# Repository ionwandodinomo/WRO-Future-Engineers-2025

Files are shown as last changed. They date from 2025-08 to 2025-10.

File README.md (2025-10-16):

<br>

Engineering Documentation 🛠️
======

<br>

> This repository details Team Tralalerotralala's building and programming process in the 2025 WRO Future Engineers Competition.

---

<br>

## Content of Repository 📘
* `models` - 3D CAD files
* `others` - Other essential files
* `schemes` - Electrical schematics
* `src` - Main and other programs to run/control software
* `t-photos` - Team photos
* `v-photos` - Robot photos
* `video` - Video demonstration

<br>

## Content of Documentation 📖
* **[The Team](#the-team-boygirlboy)**
* **[Mechanical Breakdown :wrench:](#mechanical-breakdown-wrench)**
  	* [Materials List](#materials-list)
  	* [Printed Parts](#3D-printed-parts)
  	* [Assembly Views](#full-assembly-views)
* **[Mobility Management :car:](#mobility-management-car)**
	* [The Chassis](#the-chassis)
	* [Drive System](#drive-system)
	* [Steer System](#steer-system)
* **[Power and Sense Management :zap:](#power-and-sense-management-zap)**
	* [The Battery](#the-battery)
	* [Electrical Wiring](#electrical-wiring)
	* [The Sensors](#the-sensors)
* **[Software :computer:](#software-computer)**
    * [Sensing](#sensing)
	* [Open Challenge](#open-challenge)
	* [Obstacle Challenge](#obstacle-challenge)
* **[Assembly Instructions](#assembly-instructions)**
* **[Youtube Videos](#youtube-videos)**
<br>

## The Team :boy::girl::boy:
<p align="center">
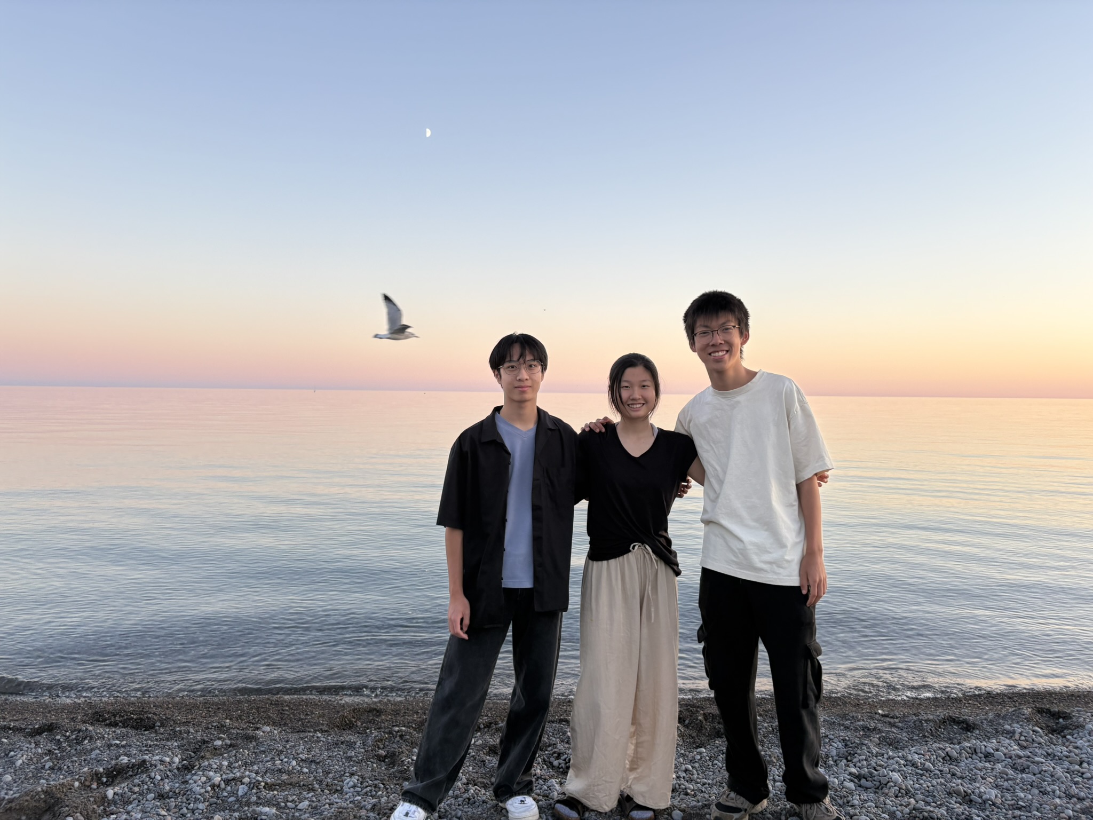
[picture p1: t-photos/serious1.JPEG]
	 
  <br>
  <em>Serious Photo</em>
</p>

### Team Members
 - John Weng (left)
 - Sunni Xue (middle)
 - Eric Rao (right)

|  | Funny Photos |  |
|:---:|:---:|:---:|
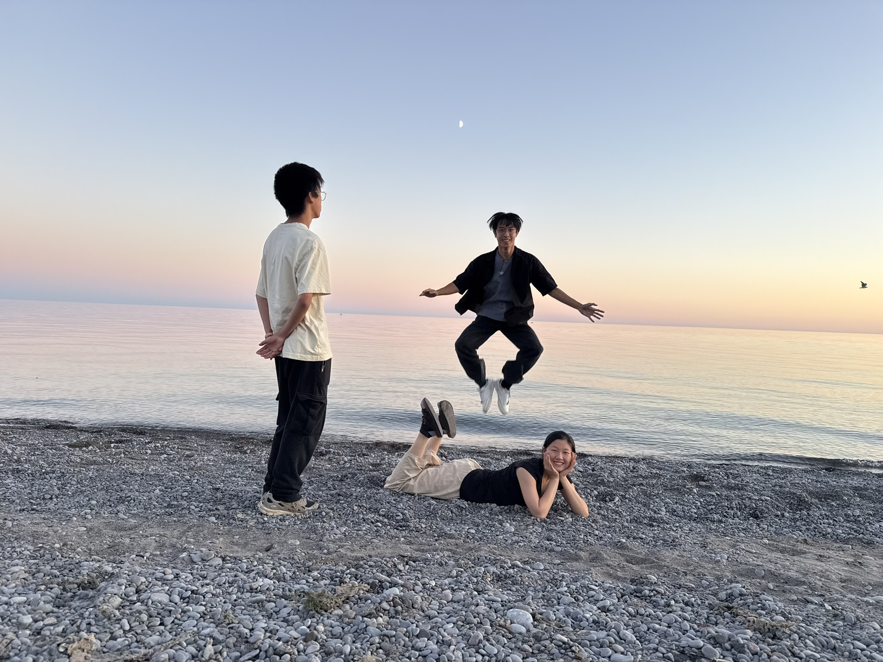
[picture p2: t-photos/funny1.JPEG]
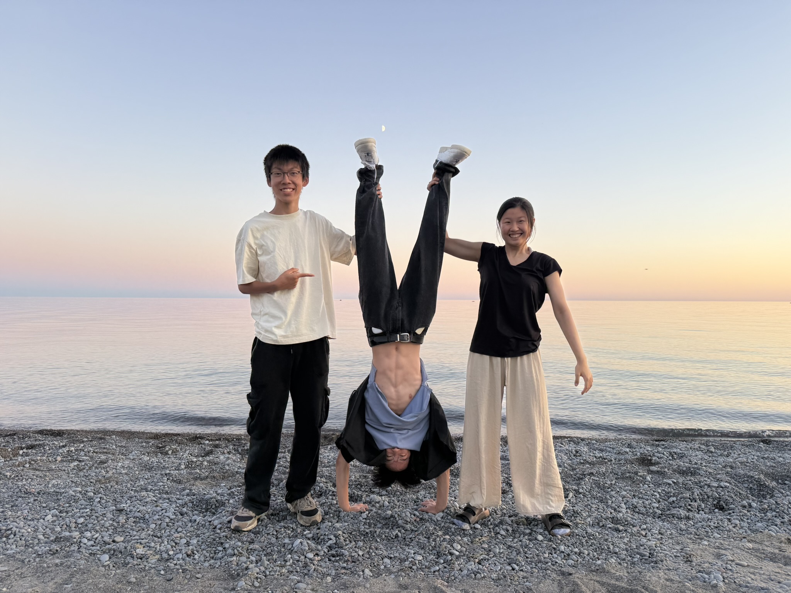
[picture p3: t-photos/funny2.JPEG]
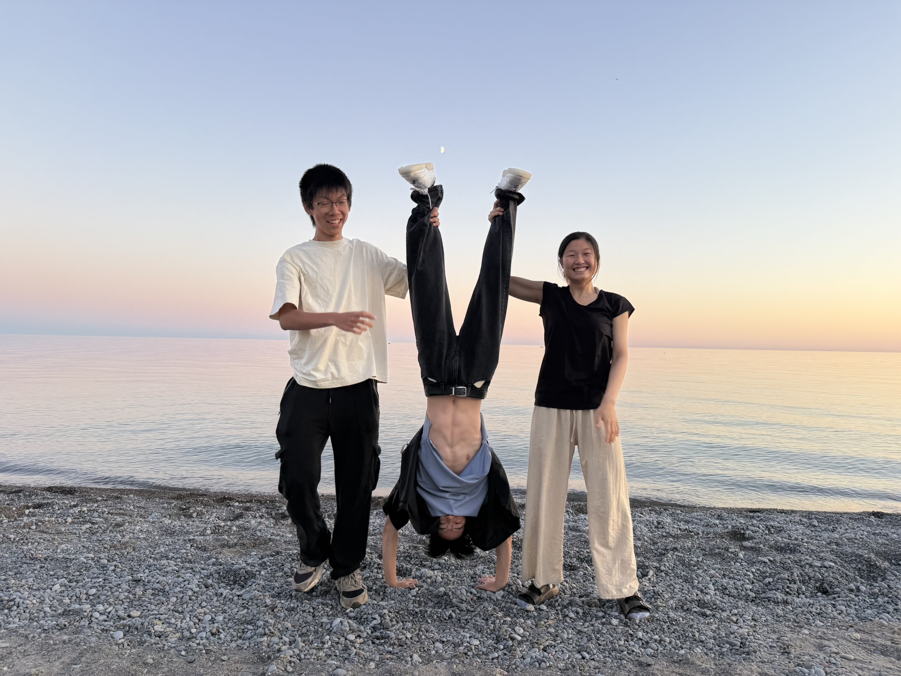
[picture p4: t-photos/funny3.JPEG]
|  |  |  |

<br>

### About us

| Name | About us |
| --- | --- |
| John Weng | Hey! I'm a grade 12 student from Maple High School in Ontario, Canada, and this is my second year doing the Future Engineers Category for WRO. I love messing with mechanics and designing solutions to problems. I love playing sports, especially badminton and volleyball. |
| Sunni Xue | Hi, I'm a grade 11 from the GTA! I've been coding since 6th grade, where I learned Python to build my first project. In my free time, I love playing sports and reading :) |
| Eric Rao | Hello, I am a 12th grade student at Anderson CVI! This is my third year back, and I'm super excited about designing, modelling, and building things. In the future, I hope to pursue mechatronics at the University of Waterloo. |

## Mechanical Breakdown :wrench:

<br>

### Materials List

| Component | Type/Category | Link / Notes |
|:---:|:---:|:---|
| Raspberry Pi 5 (8 GB) | SBC / Processor | — |
| RRC Lite Controller | Controller | [Link](https://www.hiwonder.com/products/rrc-lite?srsltid=AfmBOorP3iSszjlniFgA0gsbfA9aUH3UK0MWuyPeuTUcW6RMQjcizhmE) |
| GT24 B Differential Gear Set | Mechanical / Drive | [Link](https://carisma-shop.com/collections/gt24-spares/products/gt24-b-differential-gear-set) |
| GT24 B Spur Gear 58t | Mechanical / Drive | [Link](https://carisma-shop.com/collections/gt24-spares/products/gt24-b-spur-gear-58t) |
| GT24 SUBARU WRC WHEELS & TIRES SET | Drive | [Link](https://carisma-shop.com/collections/gt24-spares/products/gt24-subaru-wrc-wheels-tires-set-mounted) |
| GT24 WHEEL Outdrive Set | Drive| [Link](https://carisma-shop.com/collections/gt24-spares/products/gt24-b-axle-outdrive-set) |
| GT24 B Plastic Wheel lock nut set | Drive | [Link](https://carisma-shop.com/collections/gt24-spares/products/gt24-b-plastic-screw-on-wheel-nuts-x4) |
| Furitek Micro Komodo 1212 3450KV Brushless Motor | Motor | [Link](https://furitek.com/products/furitek-micro-komodo-1212-3456kv-brushless-motor-with-15t-steel-pinion-for-fury-wagon-fx118) |
| Furiteck Lizard Pro 30A/50A Brushless ESC | ESC | [Link](https://furitek.com/products/combo-of-furitek-lizard-pro-30a-50a-brushed-brushless-esc-for-axial-scx24-with-bluetooth) |
| Gens Ace 2S1P 1300mAh 7.4V battery | Battery | [Link](https://www.adrenalinehobby.com/products/gens-ace-g-tech-1300mah-2s-7-4v-25c-lipo-deans-plug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) |
| Sun Founder SG90 Micro Digital 9G Servo Motor | Servo | [Link](https://www.sunfounder.com/products/sg90-micro-digital-servo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) |
| Mini Rocker Switch | Switch | (Any switch will work) |
| Raspberry Pi Camera Module 8 MP | Sensor / Camera | [Link](https://www.amazon.ca/TUOPUONE-Compatible-Raspberry-MIPI-CSI-Interface/dp/B0CPTPJLXL?th=1) |
| Micro SD card | Storage | — |
| LDRobot LD19 lidar kit | Sensor / Lidar | [Link](https://www.aliexpress.com/item/1005003012681021.html?spm=a2g0o.order_list.order_list_main.11.7a3b18028WK12R) |

<br>

---

<br>

Our car uses primarily **3D printed PLA filament** as the structural material. We used the **[Prusa MK4S](https://www.prusa3d.com/product/original-prusa-mk4s-3d-printer-5/)** from Prusa Research, as well as the ENDER 3 S1. 3D printing allows precise designing of parts, and PLA is readily available and easily accessible for commercial 3D printing. After assessment, it was chosen over other materials such as ABS or PETG. These filaments are also all generally lighter and much more customizable than other common materials, such as LEGO.

<br>

| Material | Pros | Cons |
|---|---|---|
| **PLA** | - Easy to print<br>- Accurate <br>- Available<br>- Good surface finish | - Brittle<br>- Low heat resistance|
| **ABS** | - Strong<br>- Heat resistant<br>- Slightly flexible | - Warps easily<br>- Emits fumes<br>- Harder to print |
| **PETG** | - Strong<br>- Decent heat resistance<br>| - Stringing issues<br>- Slower prints<br>- Less precise |
| **Nylon** | - Very durable| - Hard to print<br>- Hygroscopic (*retains moisture*) <br>- High temp needed |
| **Carbon Fiber Filaments** | - Rigid<br>- Lightweight<br>- Strong | - Expensive<br>- Requires special setup<br>- Brittle |

<br>

In this particular environment, the cons of PLA aren't drastically impactful. The robot will not have to endure high temperatures, and load-bearing/flexibility is not a priority.

<br>

--- 

<br>

Our CAD softwares of choice were **[Onshape](https://www.onshape.com/en/)**, as well as **[TinkerCAD](https://www.tinkercad.com/)** for simpler geometry. We strongly recommend these two softwares programs for basic component design, as they are generally easy to learn, and provide convenient online cloud storage.

Provided below are models of the 3D printed parts, individually, as well as on the final car. Note the .stl files can all be found in the `models` folder of this repository.

<br>


### 3D Printed Parts  

<table>
  <tr>
    <td align="center" width="25%">
      <b>Axel Servo Holder</b><br>
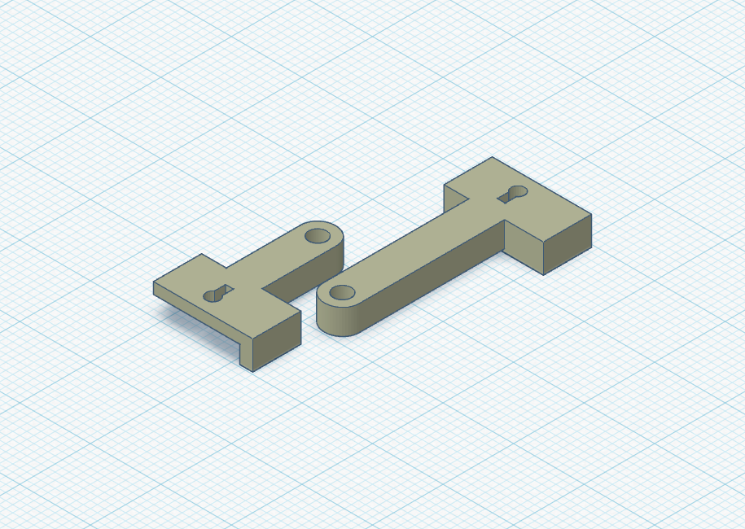
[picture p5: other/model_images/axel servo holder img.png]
      
    </td>
    <td align="center" width="25%">
      <b>Base Plate</b><br>
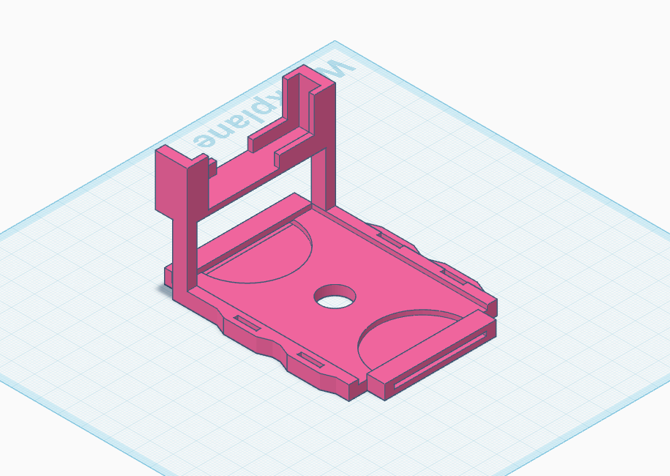
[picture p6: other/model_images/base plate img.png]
      
    </td>
    <td align="center" width="25%">
      <b>Battery Bracket</b><br>
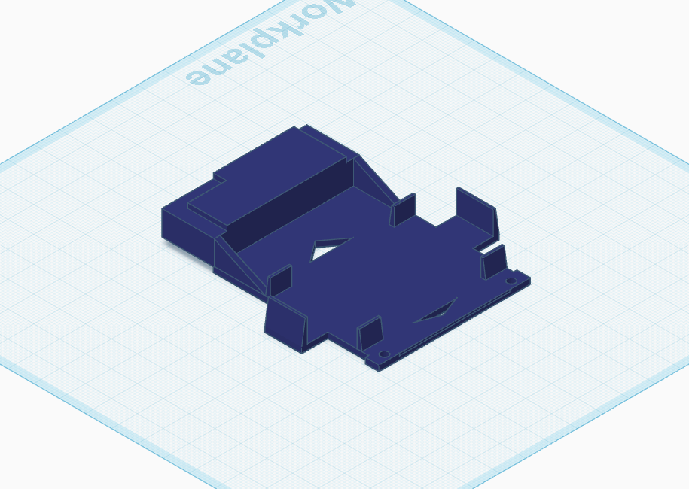
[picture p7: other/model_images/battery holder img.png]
      
    </td>
    <td align="center" width="25%">
      <b>Camera Bracket</b><br>
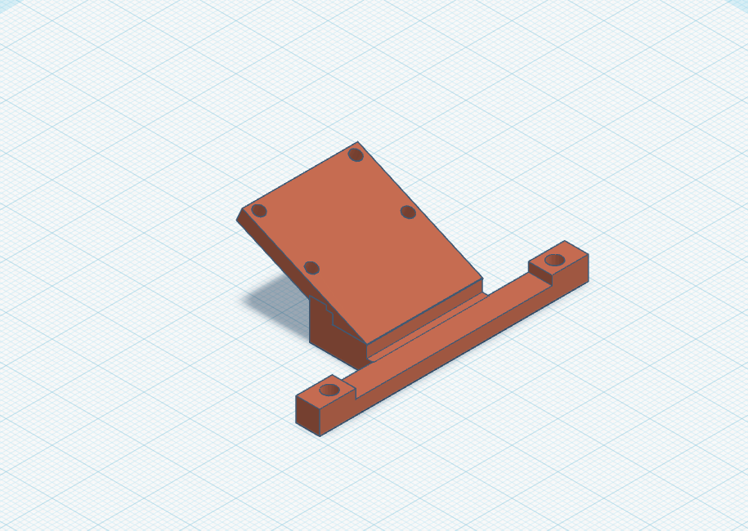
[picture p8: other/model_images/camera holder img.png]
      
    </td>
  </tr>
  <tr>
    <td align="center" width="25%">
      <b>Chassis Pin</b><br>
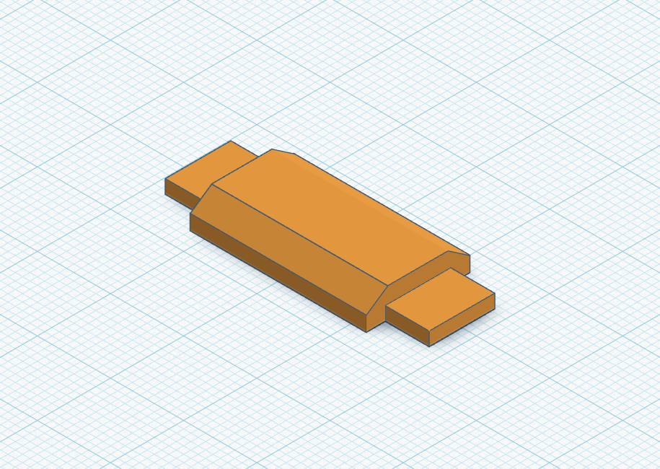
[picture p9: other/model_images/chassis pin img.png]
      
    </td>
    <td align="center" width="25%">
      <b>Differential Cover</b><br>
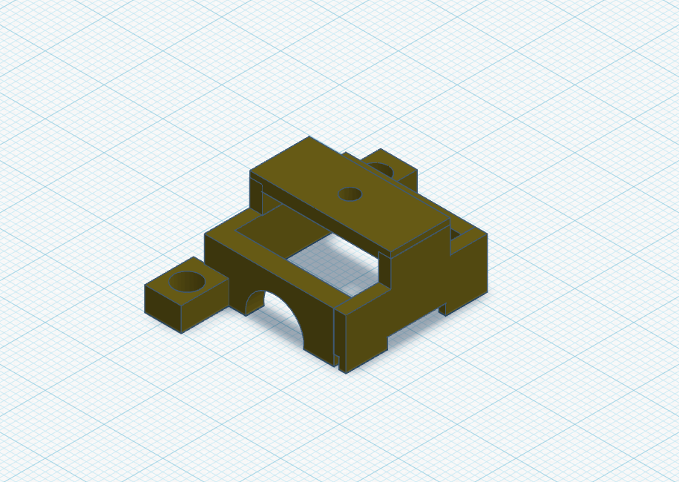
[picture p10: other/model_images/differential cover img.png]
      
    </td>
    <td align="center" width="25%">
      <b>Front Axel</b><br>
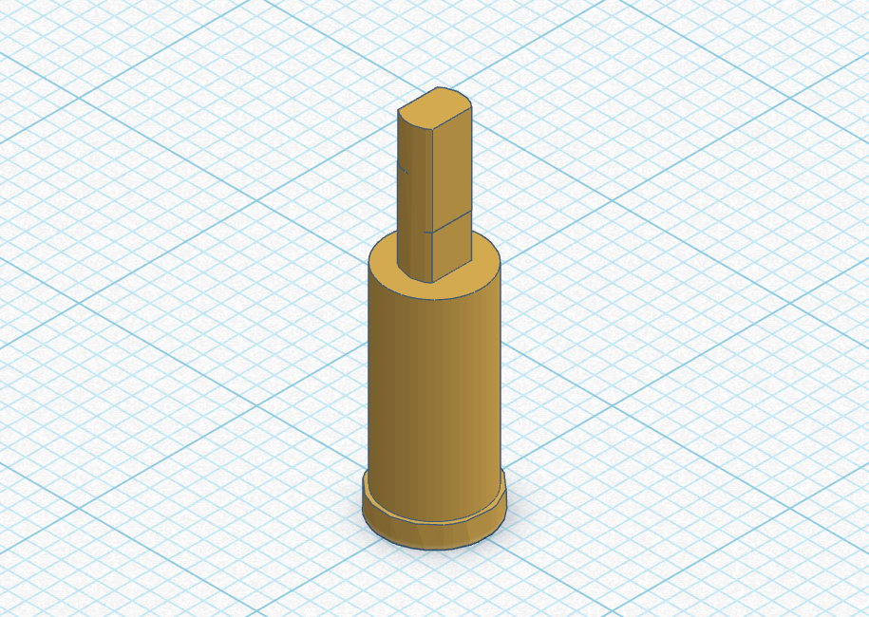
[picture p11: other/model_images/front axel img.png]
      
    </td>
    <td align="center" width="25%">
      <b>Motor Gear Bracket</b><br>
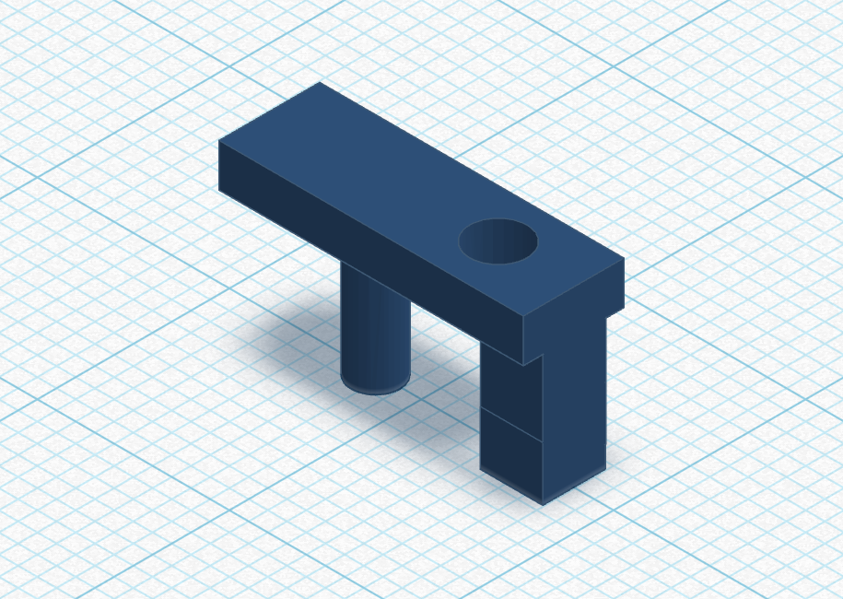
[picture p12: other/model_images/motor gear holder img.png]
      
    </td>
  </tr>
  <tr>
    <td align="center" width="25%">
      <b>Rear Motor Stand</b><br>
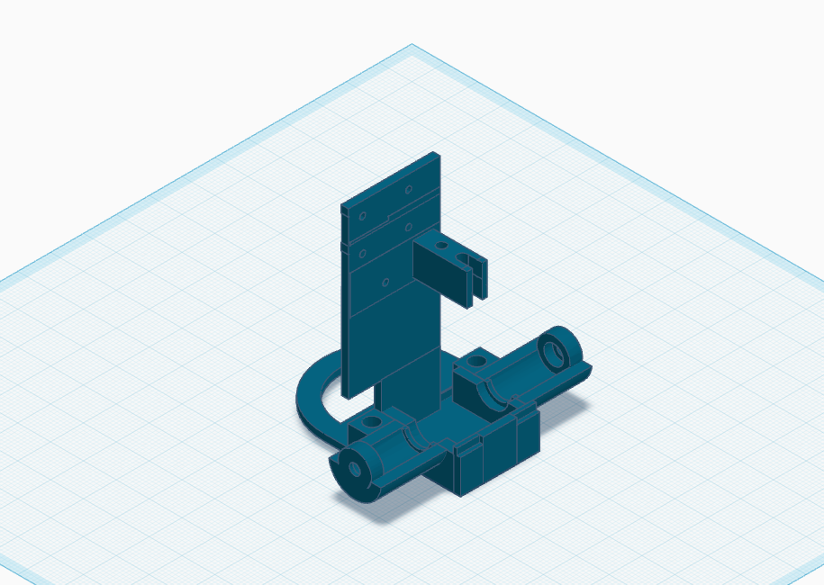
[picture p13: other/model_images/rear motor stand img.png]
      
    </td>
    <td align="center" width="25%">
      <b>RPI Base</b><br>
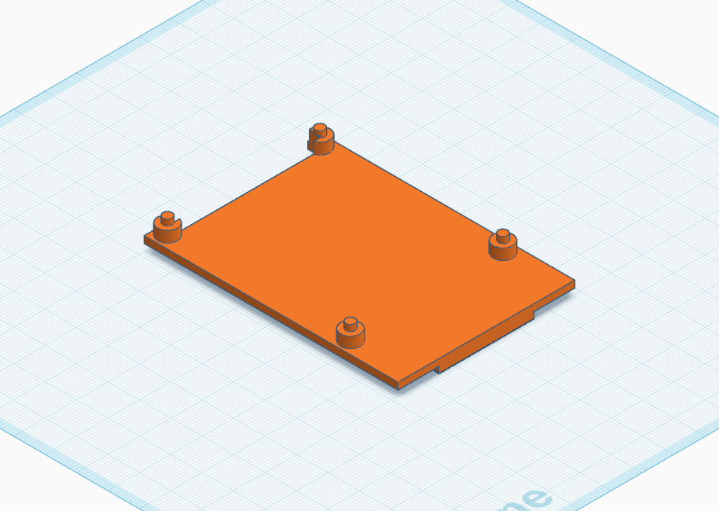
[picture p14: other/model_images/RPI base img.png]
      
    </td>
    <td align="center" width="25%">
      <b>RPI HAT Bracket</b><br>
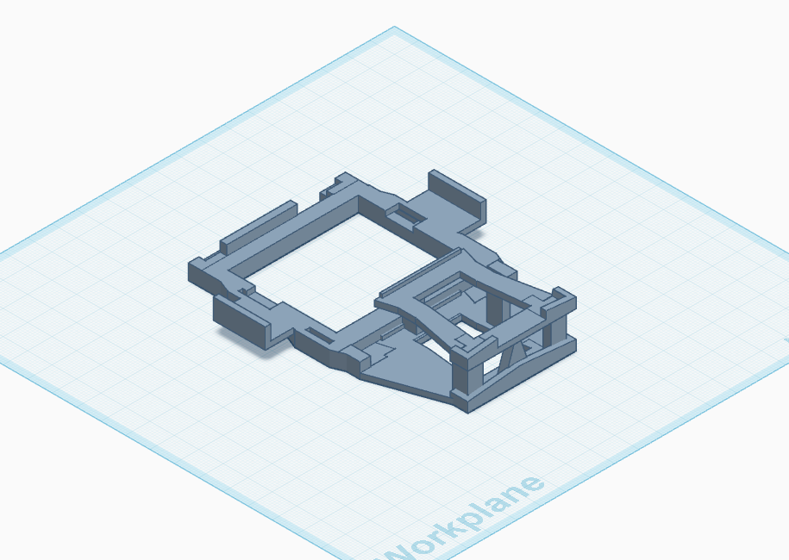
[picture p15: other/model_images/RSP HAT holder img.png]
      
    </td>
    <td align="center" width="25%">
      <b>Servo Stand<b><br>
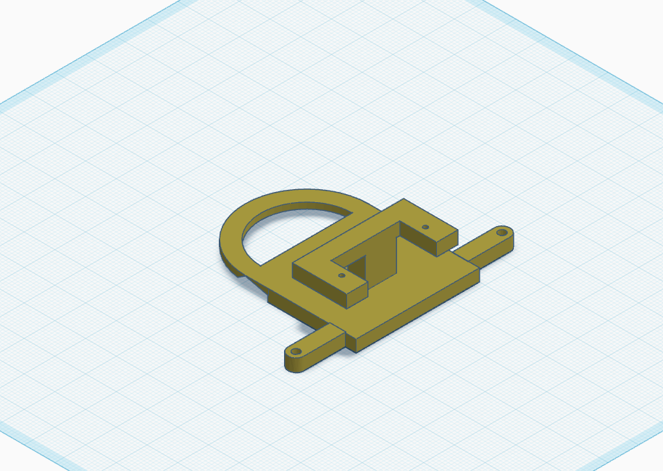
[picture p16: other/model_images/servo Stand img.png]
      
    </td>
  </tr>
  <tr>
    <td align="center" width="25%">
      <b>Wheel Bearing Bracket</b><br>
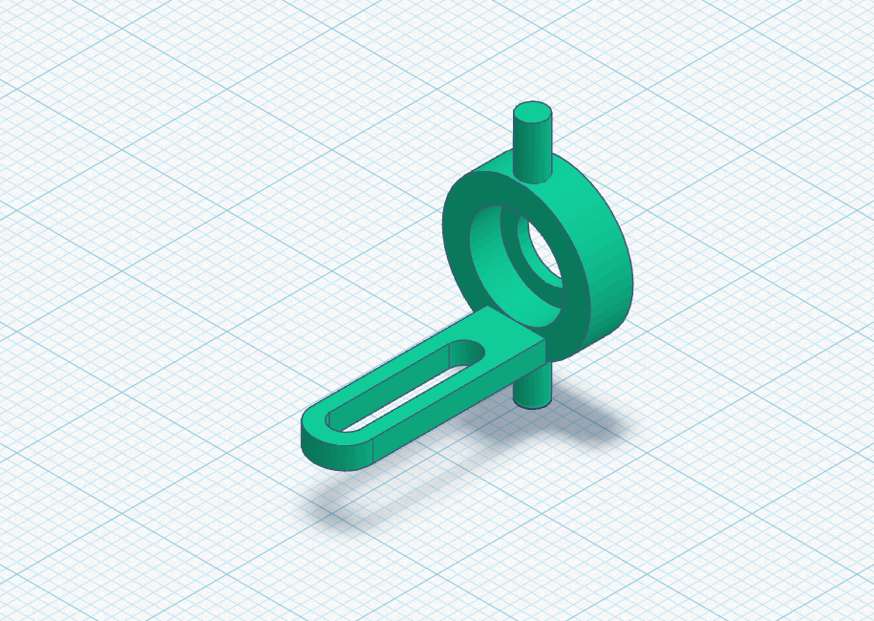
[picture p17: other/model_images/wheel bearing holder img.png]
      
    </td>
    <td align="center" width="25%">
      <b>Wheel Wrench (tool)</b><br>
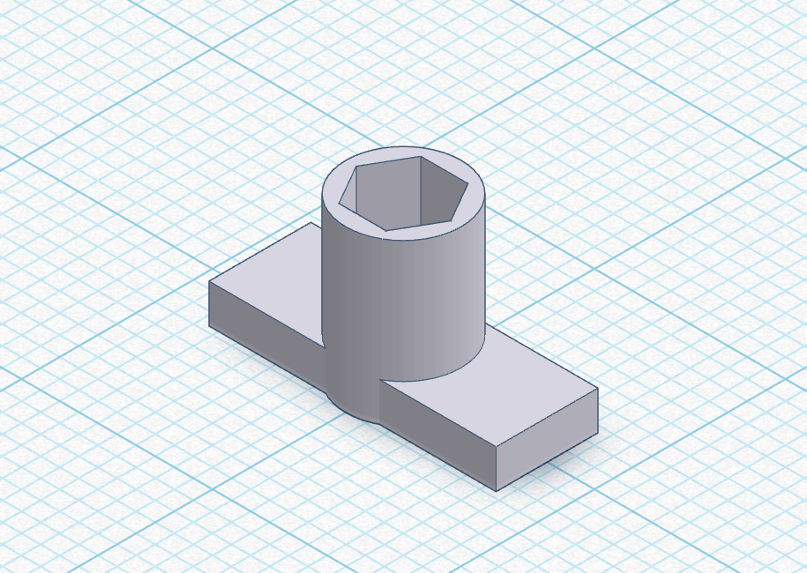
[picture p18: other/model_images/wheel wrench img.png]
      
    </td>
    <td align="center" width="25%">
      <b>Servo Horn</b><br>
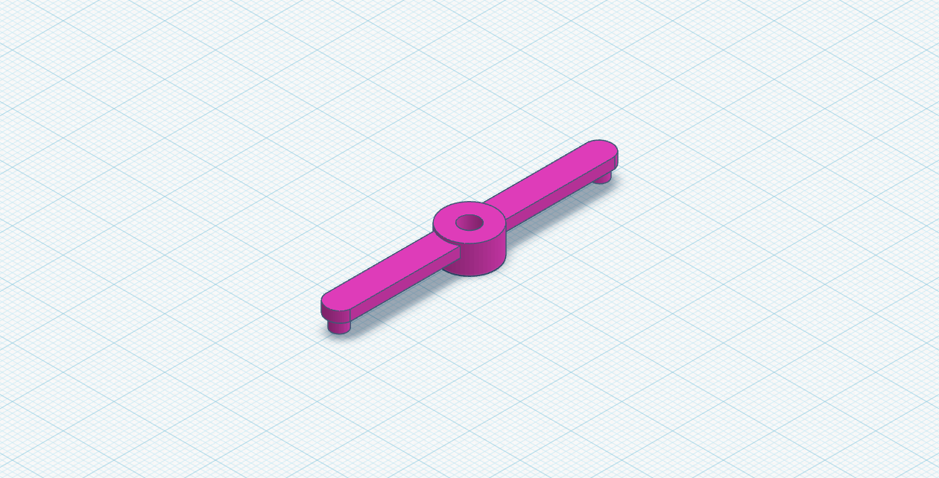
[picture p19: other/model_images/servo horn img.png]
      
    </td>
    <td align="center" width="25%">
      <b>ISO All Models </b><br>
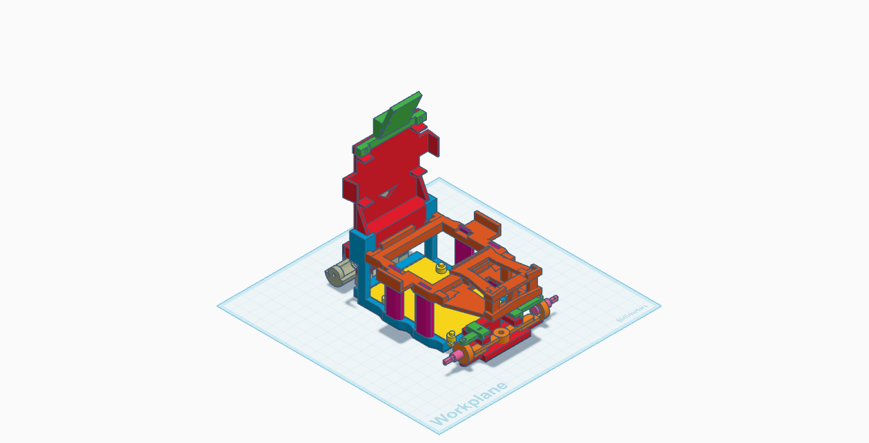
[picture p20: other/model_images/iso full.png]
      
    </td>
  </tr>
</table>  

---

<br>

### Full Assembly Views  

#### Printed Assembly  

<table>
  <tr>
    <td align="center" width="33%">
      <b>Front View</b><br>
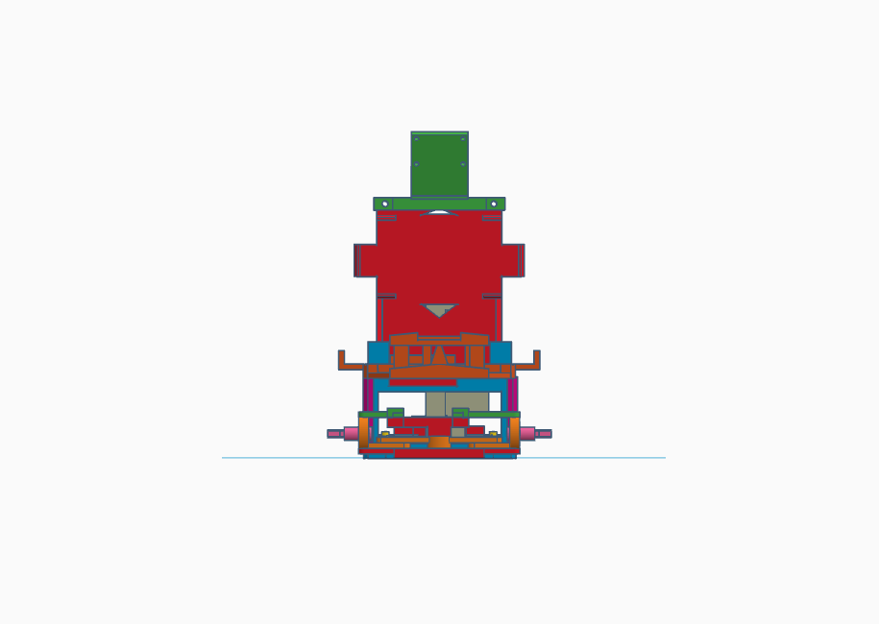
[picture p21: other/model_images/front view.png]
      
    </td>
    <td align="center" width="33%">
      <b>Back View</b><br>
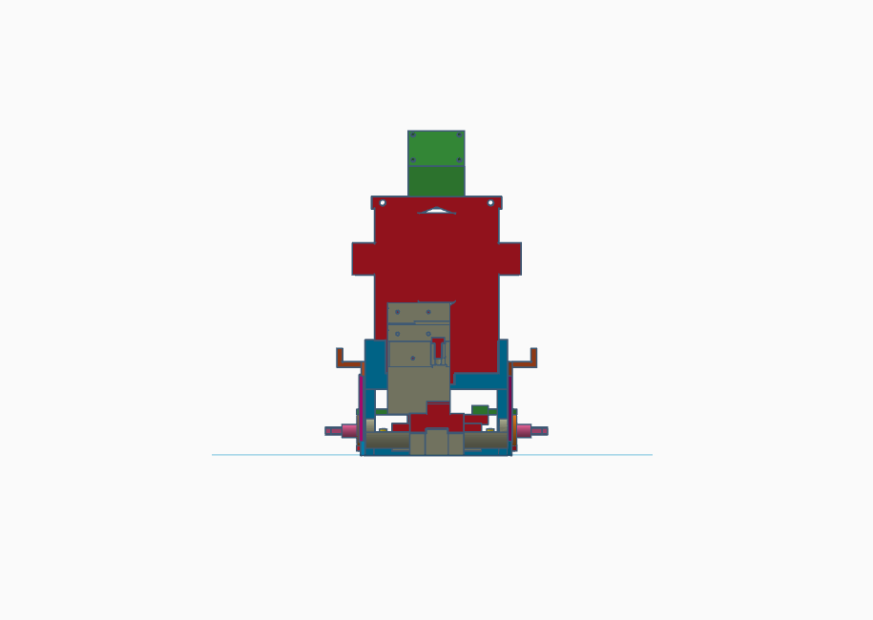
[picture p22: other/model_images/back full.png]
      
    </td>
    <td align="center" width="33%">
      <b>Side View</b><br>
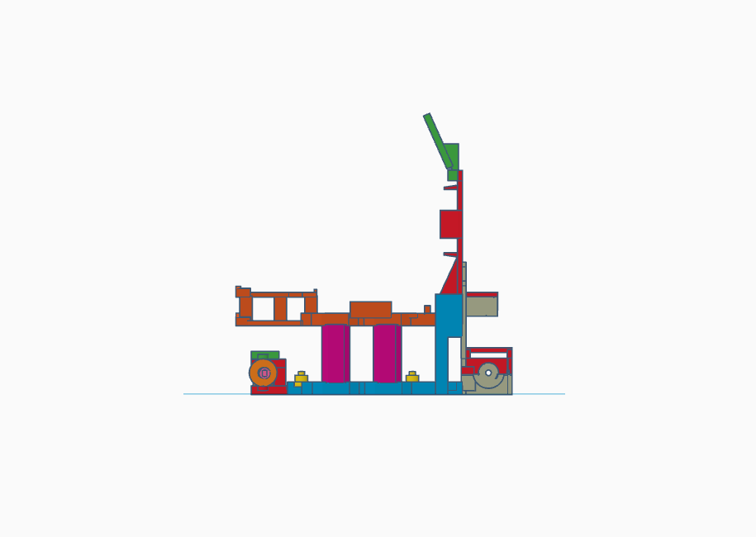
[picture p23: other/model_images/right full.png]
      
    </td>
  </tr>
  <tr>
    <td align="center" width="33%">
      <b>Top View</b><br>
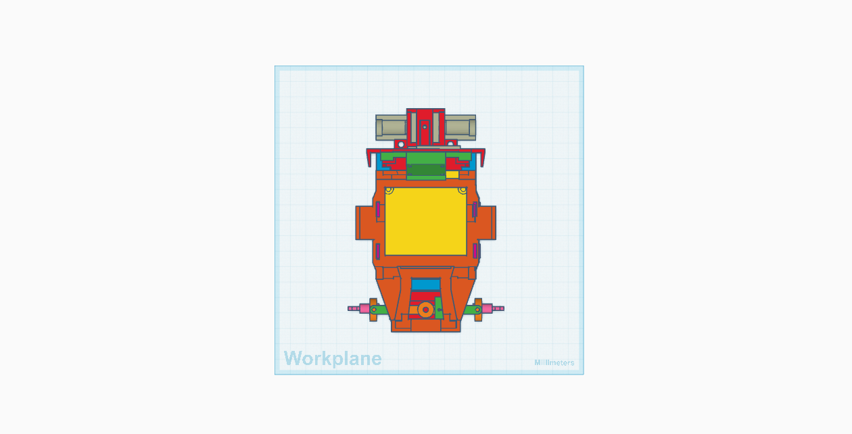
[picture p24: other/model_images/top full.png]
      
    </td>
    <td align="center" width="33%">
      <b>Isometric View</b><br>
      
    </td>
    <td align="center" width="33%">
      <b>Isometric View (back)</b><br>
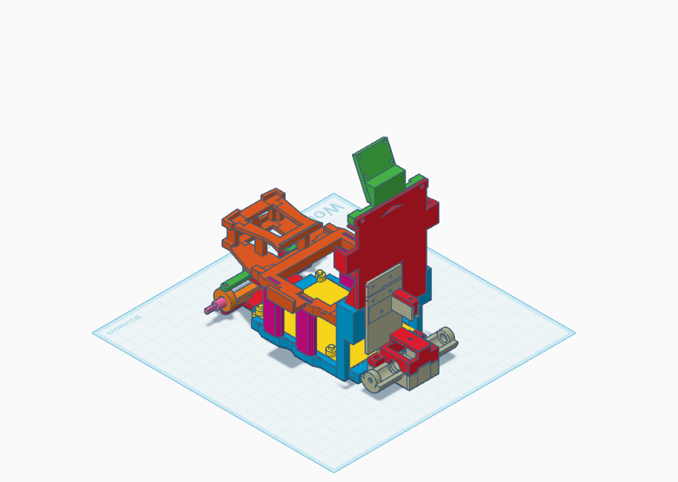
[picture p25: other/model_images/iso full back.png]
      
    </td>
  </tr>
</table>  

<br>

#### Full Assembly (with Components)

| Top | Bottom | Front |
|:---:|:---:|:---:|
|  |  |  |

| Back | Left | Right |
|:---:|:---:|:---:|
|  |  |  |

These parts were designed with **modularity** in mind, meaning each section of the car can function more or less individually. They piece  smoothly as separate parts, instead of a single printed chassis, as originally planned. Screws were avoided as much as possible, as they are less reflective of this idea, but regardless used when necessary. 

<p align="center">
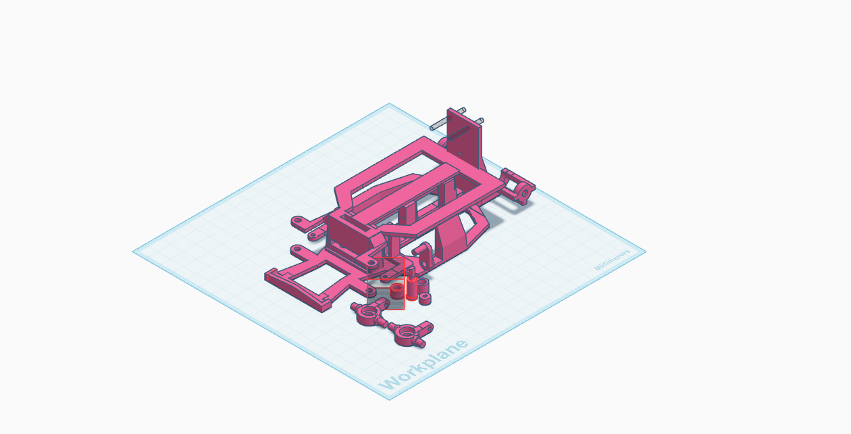
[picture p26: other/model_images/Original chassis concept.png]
  
  <br>
  <em>Original concept of a single chassis plate</em>
</p>

We found this approach much more convenient while testing, as it allows for changes to be made to a specific part of the car, and easily replaced and updated without collateral impact to the rest of the body. In other words, an **iterative** approach.

<br>

### Possible Improvements
- Upgrading print system to include **PETG** or **carbon fiber** filaments for more durable, high-quality parts.
- Changing connection points to **snap-fits**, **press-fits**, etc, rather than screws, to simplify maintenance and quick iteration.
- Optimized print orientation to reduce warping and the need for potentially inaccurate supports.

<br>

---

<br>

## Mobility Management :car:

For the use of this competition, movement precision and responsiveness are the top priorities.

---

<br>

### The Chassis
The chassis is located in the center of the car. It provides a strucutre to lay the majority of electrical components onto, namely the **two boards** as well as the **LIDAR**. It also serves as a medium to connect the front and rear wheel systems. The chassis itself is split into two separate plates that align together to form the abdomen of the car.

<br>

#### Chassis Models
<table>
  <tr>
    <td align="center" width="33%">
      <b>Main Plate</b><br>
      
    </td>
    <td align="center" width="33%">
      <b>Connective Plate</b><br>
      
    </td>
    <td align="center" width="33%">
      <b>Together</b><br>
      
    </td>
  </tr>
</table>

<br>

Again, the choice of 3D printed PLA filament allows this precise jointery of components. They fit snugly together, and the friction also helps keep tight connection points along the entirety of the chassis. 

After some trials with the 3D printer, our final print settings include a **0.4mm nozzle**, **~50% infill**, **brim disabled**, and **snug** supports. These specific choices enable a sturdy, slightly flexible base and remove the "junk" filament that might otherwise be printed with brim enabled or other kinds of supports.

Another consideration improving the **balance** of the robot, which directly influences the consistency of our movement. Two vital aspects are maintaining a low, as well as a centered point of mass. In another words, keeping our components, particulary the heavy ones, as low and as centralized as possible. For example, the boards, which are located at the very base and center of the car.

<br>

<p align="center">
  Previous Version
  <br>
  <em>Location of the Raspberry Pi</em>
</p>

<br>

#### Camera Mount

<table>
  <tr>
    <td width="50%">
      One restriction to take into account is the minimum height instated by the <b>camera</b>.  
      <br><br>
      We found that it had to be placed fairly high up, with a generous angle downwards, in order to consistently capture all the challenge objects.  
      <br><br>
      A <b>modular</b> design was implemented to test with different heights and angles, but the consequence of a high center of mass was left overlooked.  
    </td>
    <td width="50%" align="center">
      
    </td>
  </tr>
</table>  

<br>

#### Possible Improvements
- Optimizing the location of our components, such as lowering the **LIDAR** or centralising the **battery** for an ideal center of mass.
- Adding **suspension** or other shock-absorbent materials for steadier and reliable conditions for the sensors
- Design a housing to protect sensitive components from dust or other external debris.
- Lowering the height of the camera, perhaps by using a more **LIDAR** dominant approach.

<br>

---

<br>

### Drive System

The robot features a **rear-wheel drive (RWD)** layout powered by the **Furitek Micro Komodo Motor**, paired with the **Furitek Lizard Pro ESC**. A **12:58 gear ratio** was selected to optimize torque delivery for obstacle navigation.  

<br>

#### Why Rear-Wheel Drive?  
- **Lightweight Drive System**: The front wheels remain free for a simpler, lighter system.  
- **Efficient Transfer**: Torque from the motor is delivered directly to the gearbox, minimizing drivetrain energy losses.  
- **Modularity**: Allows swapping motor mounts and experimenting with different gear ratios without redesigning the entire chassis.  

<br>

#### Motor Specifications

<table>
  <tr>
    <td align="center" width="50%">
      <b>Furitek Micro Komodo Motor</b><br>
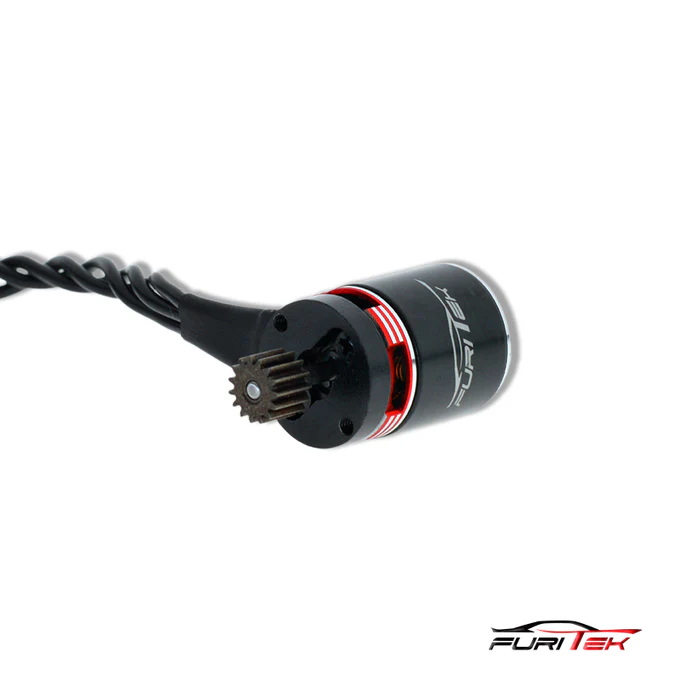
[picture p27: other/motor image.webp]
      
    </td>
    <td align="left" width="50%">
      <ul>
        <li><b>Type:</b> Brushless DC Motor</li>
        <li><b>Voltage:</b> 7.4V nominal</li>
        <li><b>Max Current Draw:</b> ~5A</li>
        <li><b>ESC:</b> Furitek Lizard Pro</li>
        <li><b>Gear Ratio:</b> 12:58</li>
        <li><b>Drive Layout:</b> Rear-Wheel Drive (RWD)</li>
      </ul>
    </td>
  </tr>
</table>  

<br>

---

<br>

#### Mounting and Layout  

- Motor secured to the **rear chassis plate**
- Stock differential gear system and gear are attached, so that a **gear-down** ratio is implemented.
- This improves our robot's performance at low speeds, which is particularly important during the turning in the obstacle challenge.
- The axles, bearings and wheels are added afterwards.

<br>

#### Possible Improvements
- Upgrade to metal gears to combat wear from heavy, high-speed usage.
- Experimenting with different gear ratios. Combinations close to **12:58**, such as 14:58 or 10:58, may provide a better balance between torque and maximum speed.
- Upgrading or lubricating bearings for less friction and a higher efficiency/consistency.

<br>

---

<br>

### Steer System

<table>
  <tr>
    <td align="center" width="50%">
      <b>SG90 Servo</b><br>
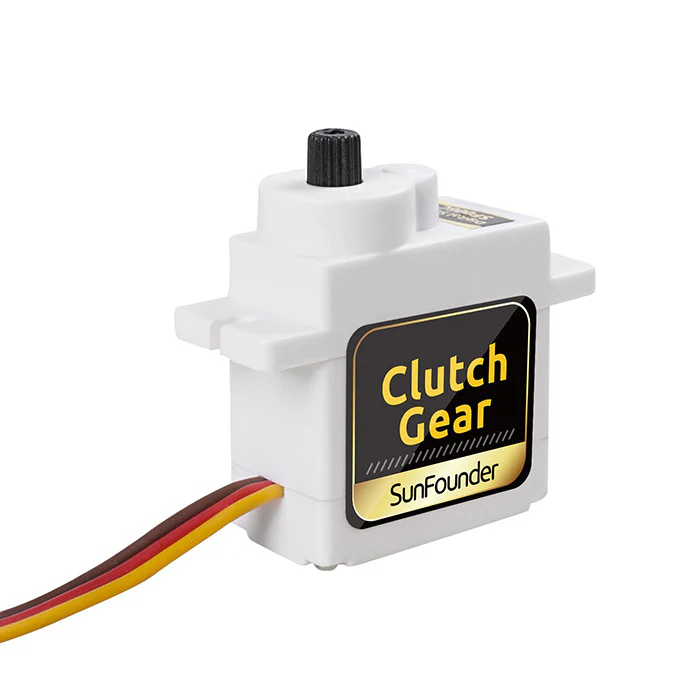
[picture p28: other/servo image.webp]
      
    </td>
    <td align="left" width="50%">
      <ul>
        <li><b>Weight:</b> 9 grams</li>
        <li><b>Dimensions:</b> 23mm x 12.2mm x 29mm </li>
        <li><b>Operating Voltage:</b> 4.8V - 6V DC</li>
		<li><b>Gear Type:</b> Nylon gear set</li>
		<li><b>Speed:</b> 0.10 - 0.12 secs per 60 degrees</li>
      </ul>
    </td>
  </tr>
</table>  

The steering system is comprised of 3, 3D printed components. This includes the servo horn, wheel pivot, and locking mechanism.

The servo motor itself is mounted onto the front chassis plate using a custom bracket. A 3D-printed servo horn is installed on the servo head for linkage connection. This specific design was chosen for 3 main reasons: it's **simplicity**, **space efficiency**, and **printability**.  

There is only one point of contact between the servo and the wheel, which greatly improves the reliability of the system. More complex designs may allow for extremely precise steering, but sacrifice the "directness" of a design like this. The lack of complicated geometry also makes it very easy to print, even on lower-end 3D printers.

The locking mechanism is made up of 2 parts: the top and the bottom. These parts extend outside of the servos body and clamp the turning axel in place. Otherwise, the axles would not be attached to the car. 

#### Chassis Models
<table>
  <tr>
    <td align="center" width="33%">
      <b>Servo horn</b><br>
      
    </td>
    <td align="center" width="33%">
      <b>Wheel pivot</b><br>
      
    </td>
    <td align="center" width="33%">
      <b>Together</b><br>
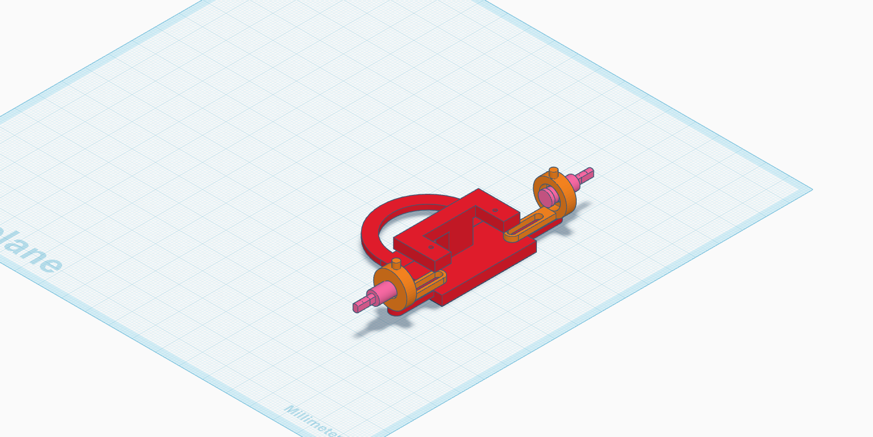
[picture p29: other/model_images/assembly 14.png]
      
    </td>
  </tr>
</table>

On top of that, this design also allows the servo to be placed directly on top of the steer system, instead of behind or in front of it. Due to the design of our car, this also saves space for our LIDAR and controller boards to be placed, and doesn't extend the length an unnecessary amount. 

Another factor is the symmetry of the design, which plays two roles. It allows the servo motor to be placed very close to the center of the robot, which is a key consideration when managing balance and the center of mass of the entire vehicle. It also ensures that the central pivot point is the exact same distance away from both wheels. This means that the same force will be applied to both sides, and so both wheels will always turn at the exact same angle.

<br>

#### Possible Improvements
- Fine-tune the servo-horn length to adjust **steering sensitivity**. There is a balance between steering precision and steering radius. An optimized ratio could lead to more sensible and more precise turning angles.
- Use metallic bearings at contact points. The current design has plastic-plastic contact, which is not nearly as dependable or frictionless as metal.
- Consider other steering mechanisms, such as **bellcrank**, and explore the tradeoffs between simplicity and accuracy.

<br>

---
<br>

## Power and Sense Management :zap:
### The Battery
The [Gens Ace 2S1P 1300mAh 7.4V battery](https://www.adrenalinehobby.com/products/gens-ace-g-tech-1300mah-2s-7-4v-25c-lipo-deans-plug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) is overkill for the power supply of our car. This battery has a continuous discharge rate of 45C, delivering more than enough power for the peak demand of our electronics, including the SG90 Servo, Furitek motor, ESC, Raspberry Pi 5 and the RRC Lite Controller. The ESC, connected directly to the controller, regulates the voltage to the motor, avoiding brownouts even under full load.

#### Power Ratings

| Component | Voltage | Max Current Draw |
|:---:|:---:|:---:|
| RRC Lite Controller | 5 V | 0.5 A |
| YDLidar T-mini | 5 V | 0.3 A |
| Furitek Micro Komodo Motor | 7.4 V | 5 A |
| Furitek Lizard Pro ESC | 8.4 V | 50 A |
| SG90 Servo Motor | 5 V | 0.25 A |
| Pi Camera | 5 V | 0.25 A |
| MicroSD, LEDs, and Speakers | 5 V | 0.2 A |

---

#### Total Power Draw

| Category | Value |
|:---:|:-----:|
| Average Current Draw | 10.5 A |
| Battery Output Capacity | 32.5 A |
| Headroom | 22 A |

### Electrical Wiring
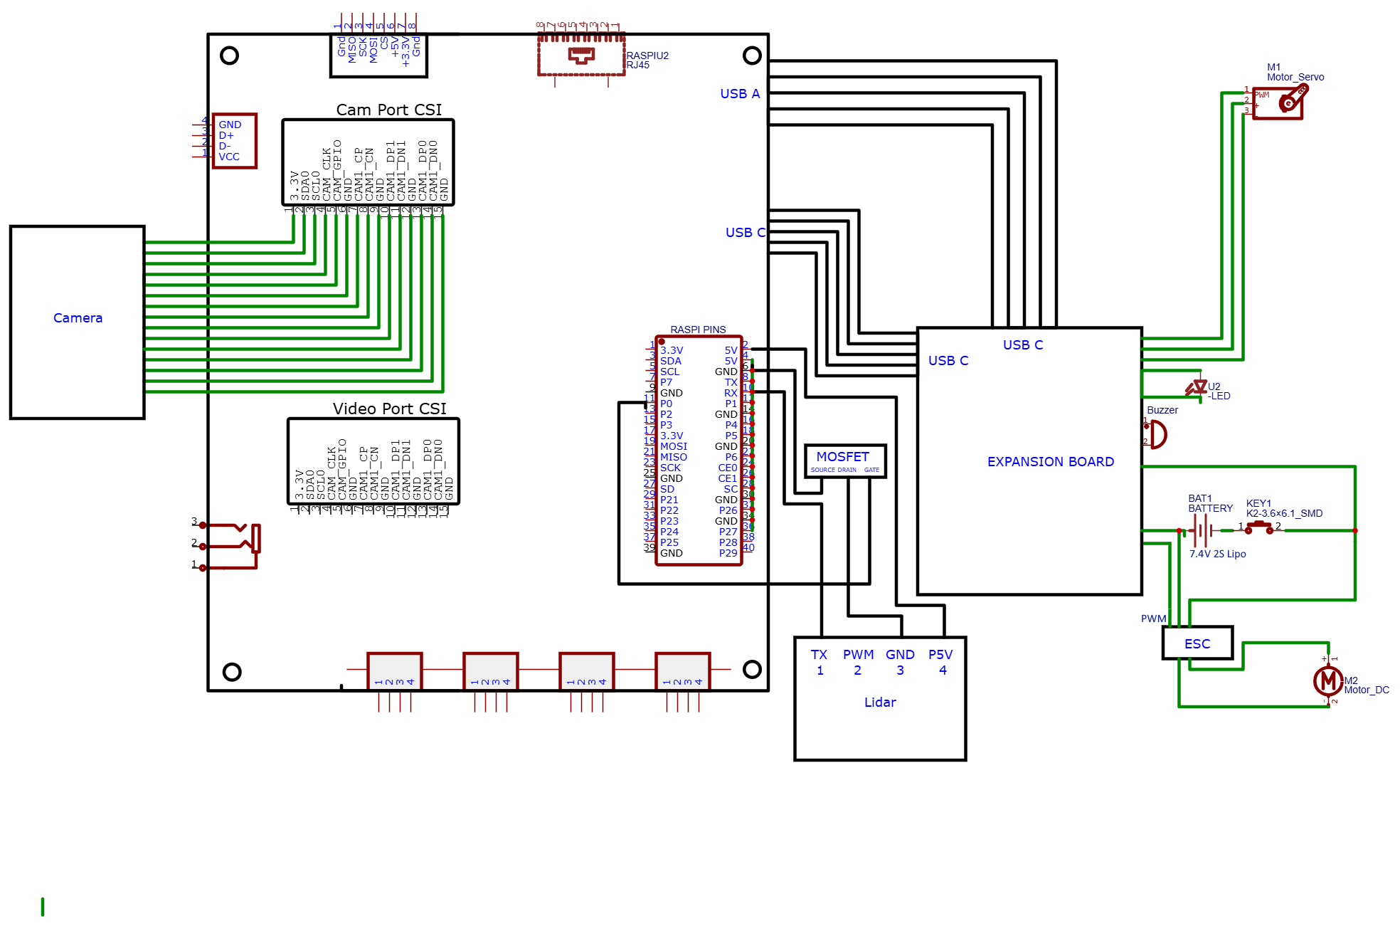
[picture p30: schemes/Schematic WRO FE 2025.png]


### The Sensors
The car gets input from the [Raspberry Pi 5 Camera Module 8 MP MIPI-CSI Interface](https://www.amazon.ca/TUOPUONE-Compatible-Raspberry-MIPI-CSI-Interface/dp/B0CPTPJLXL?th=1), the built-in gyro sensor from the Hiwonder hat, and the [LDRobot D500 lidar kit](https://www.amazon.ca/LDROBOT-Outdoor-Navigation-Scanning-Support/dp/B0DDKXQ23R). We can use these 3 in conjunction, with the camera detecting colour, walls, and the lidar detecting walls and parking spaces. The gyro sensor aids the other two sensors in the precise movements, allowing for greater control over the car.

However, these sensors give us raw values that must be processed before they can be used. The next section details each sensor's preprocessing.

<br>

## Software :computer:
### Sensing
*** note that imu and lidar are only used for parking. Obstacle challenge and open challenge only use the camera
#### IMU
The gyro (IMU) is a built-in sensor part of the Hiwonder expansion board. As part of this, data is published as a ROS2 topic node on start up. This is the data we receive when running `ros2 topic echo /imu/rpy/filtered`
```
---
header:
  stamp:
    sec: 1757283342
    nanosec: 889812767
  frame_id: imu_link
vector:
  x: -0.0479255131599775
  y: 0.021886505195461117
  z: 2.1918381606525985
---
```
For our purposes, we only need to extract the `z` value for orientation

#### Lidar
The lidar we used was a very primitive lidar without any built-in drivers. This meant we had to manually parse through the data packets sent by the sensor. After reading the development manual, this script was created to parse lidar data.
```python
ser = serial.Serial(PORT, BAUD, timeout=0.1)
buffer = bytearray()
while True:
    data = ser.read(256)
    if data:
        buffer += data
        while True:
            idx = find_packet_start(buffer) # please refer to /src for the specifics of this function
            if idx == -1 or len(buffer) - idx < PACKET_LEN:
                break
            packet = buffer[idx:idx+PACKET_LEN]
            buffer = buffer[idx+PACKET_LEN:]

            parsed = parse_packet(packet) # please refer to /src for the specifics of this function
            if parsed:
                angles = interpolate_angles(parsed["start_angle"], parsed["end_angle"], 12) # please refer to /src for the specifics of this function
                print(f"\nSpeed: {parsed['speed']:.2f} RPM | Timestamp: {parsed['timestamp']} ms")
                for i, ((dist, conf), angle) in enumerate(zip(parsed["points"], angles)):
                    print(f"  Pt {i+1:02d}: {angle:.2f}°  {dist} mm  (conf: {conf})")
            else:
                print("Invalid packet")

    time.sleep(0.01)

```
We add this data to a dictionary that holds the latest distance per angle. This way, we can access specific angles (eg, 0.0, 180.0, etc.)

#### Image Preprocessing
In both challenges, we used a Raspberry Pi camera with cv2.contours to locate the various obstacles and walls. The camera has specific regions of interest (ROIs) for each "object type", allowing us to cut out noise and unnecessary uncertain variables. Additionally, only drawing contours in specific ROIs allows us to combine ROIs to create more "fitting" shapes (eg, 2 for each wall due to perspective). 

The open challenge utilized 3 colours: black (wall), orange (line), and blue (line).
The obstacle challenge utilized 6 colours: black (wall), orange (line), blue (line), magenta (parking lot), red (pillar), green (pillar).

All issues experienced did not significantly affect the open challenge due to its simple nature.

Originally, the contours were drawn with HSV (hue, saturation, value) ranges. Each colour had one range: an upper and lower boundary. However, due to the nature of hsv, red required 2 ranges and changes in lighting proved significant for the accuracy of the contours. Additionally, distinguishing orange, red, and magenta proved challenging in certain lightings.

<p align="center">
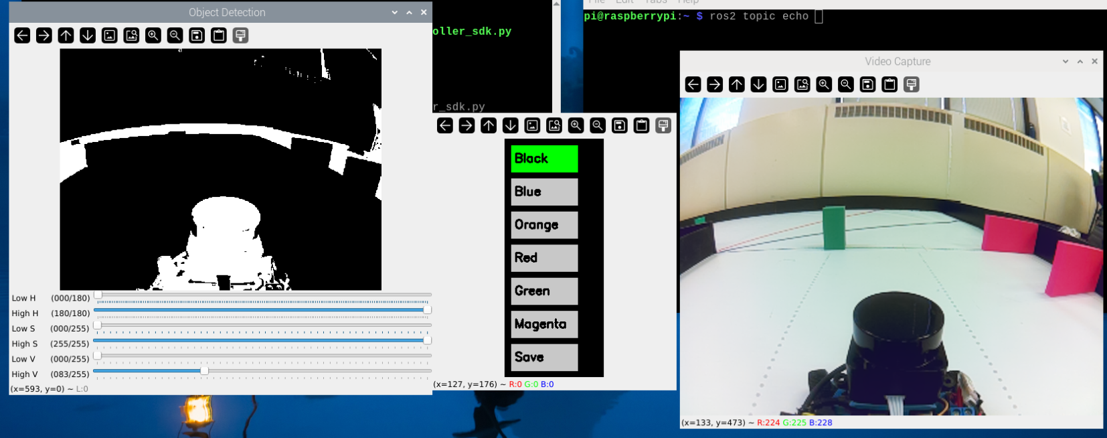
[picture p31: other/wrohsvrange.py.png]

  <br>
</p>
Since HSV ranges proved difficult, we made the switch over to LAB (lightness, red-green axis, blue-yellow axis), which is more tolerant of lighting changes. This also allowed for the red contour to only use two ranges.

In addition to the switch to LAB, several more filters were applied and tested in an effort to increase colour detection accuracy

Using these ranges, a colour mask could be created and applied to each frame. Using a mask also allowed us to combine colours in contours. For example, using the bitwise or operator, we could combine black and magenta contours to be treated as a wall when not in the parking sequence.
To increase the consistency, we switched to LAB ranges as they were more accurate when checking the hues. Most regions of interest only check for the largest contour in their region, as smaller contours are either insignificant at the point or not a part of the track.

<p align="center">
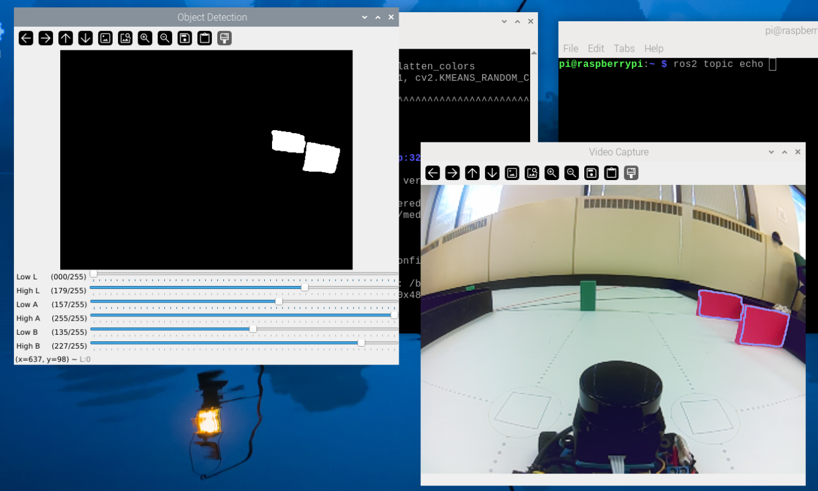
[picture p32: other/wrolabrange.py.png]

  <br>
</p>

Saturation: ❌
- We had the idea to increase the saturation of the frame by units of magnitude to increase visibility between red and orange, especially in dull lighting
- However, this messed up other colours, more specifically white, and it would show up "rainbow" due to the undertones being more visible

Filter/colour normalization: ✅
- Due to concerns with lighting, we created a mask based on the comparison between the ideal colour and the frame capture colour of the white map.
- This mask could then be applied across the entirety of the frame.
- This means if there was yellow lighting, the mask would cancel it out, etc. This also allowed auto brightness adjustment
- Additionally, this meant LAB colour ranges were more stable, with fewer changes needed day-of
<p align="center">
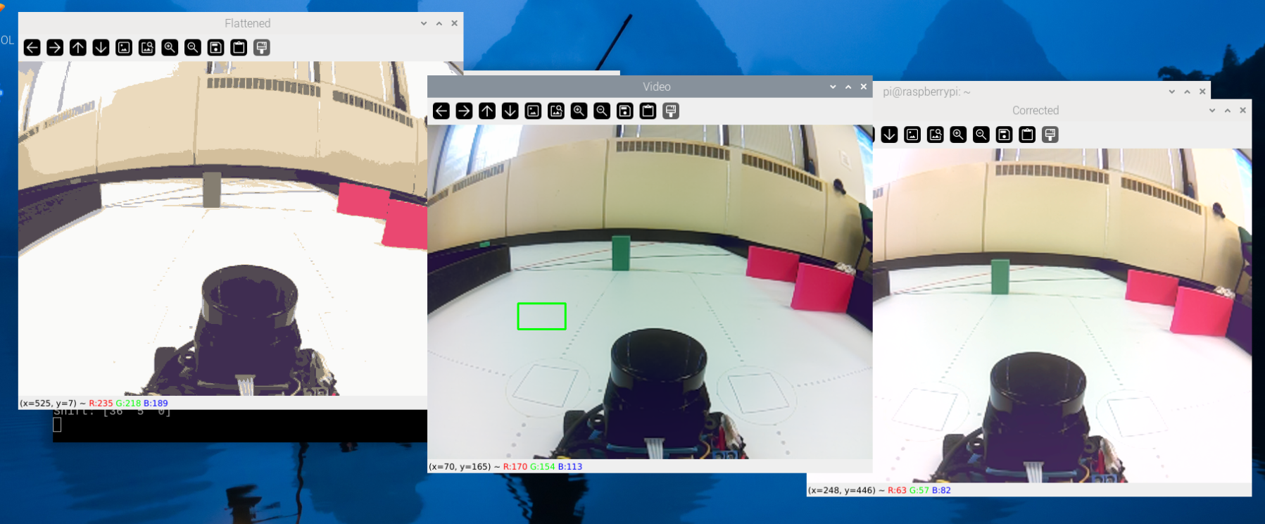
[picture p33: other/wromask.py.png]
 
  <br>
</p>

Colour flattening: ❌
- make similar colours into 1 colour, flattens the image such that shadows affect the colour less
- over-simplifies image and CPU-intensive

Unexpectedly, frame rate also played a large role in contour detection:
- It was observed/calculated that the process bottleneck was at ~64 fps
- Frame rates 25, 30, 50, 75 were tested
	- 25: too slow
 	- 30: perfect
  	- 50: messed with exposure, creating a much darker capture than reality
  	- 75: too fast
  
Camera settings:
```py
picam2 = Picamera2()
picam2.preview_configuration.main.size = (640,480)
picam2.preview_configuration.main.format = "RGB888"
print(picam2.preview_configuration.controls.FrameRate)
picam2.preview_configuration.controls.FrameRate = 75
picam2.set_controls({"Brightness": 0.05})
print(picam2.preview_configuration.controls.FrameRate)
picam2.preview_configuration.align()
picam2.configure("preview")
picam2.start()
```

### Open Challenge
#### Overview of Challenge
The open challenge is a simple round, where each team has 3 minutes to drive 3 laps autonomously on a track.  The goal of the challenge is to complete the laps as fast and consistently as possible, without touching the outer walls (inner walls may be touched without penalty).

Each round of the challenge, the wall distances are randomized, such that each straight section can is either a wide wall (100 cm) or a narrow one (60 cm). 

The wide configuration leaves a large gap between the inside and outside walls, while the narrow walls give the car much less space to manoeuvre.

The track direction is also randomized.
<p align="center">
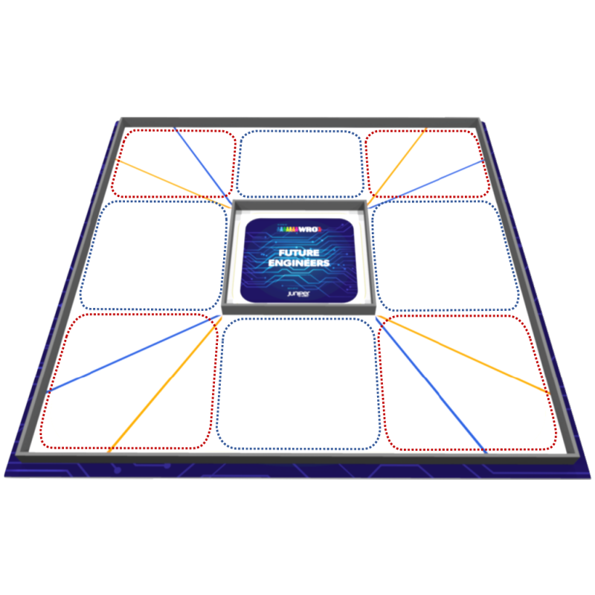
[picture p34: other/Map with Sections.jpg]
  
  <br>
  <em>Overhead view of map with sections</em>
</p>

#### Our Solution
We used just the camera to complete the open challenge. It was used for line detection and wall detection.

**ROIs are rectangles on a frame defined by the top left corner and bottom right corner <br>
To break down the challenge into manageable parts, we thought of it as three parts. These three parts are comprised of turning, driving in the straights, and counting the turns. In all three parts, six ROIs were used. Four of these regions tracked the walls, using a LAB or HSV range to check for the black colour of the walls. These ROIS were seperated by upper, lower, and left, right. ROIs of top and bottom were combined to create one larger ROI for each wall (left, right).

Black contours were extracted to return a number for the total number of pixels in each of the ROIs.

The last two regions of interest are in the very bottom left and right, used to track the blue and orange lines on the track, allowing us to ascertain the correct direction and the corners of the track. Only one of the two regions is used depending on the direction of the track.

The difficulty of the challenge stems from the variations in the track's width, particularly in the corner sections where the track transitions from narrow to wide or vice versa. This drastic change in track size, coupled with static ROIs relative to the frame, can confuse the car in some cases, creating instances where it was difficult to recognise the walls at the correct locations. The ROIs being "off" meant that the contours received were not a good representation of the car's position.
<p align="center">
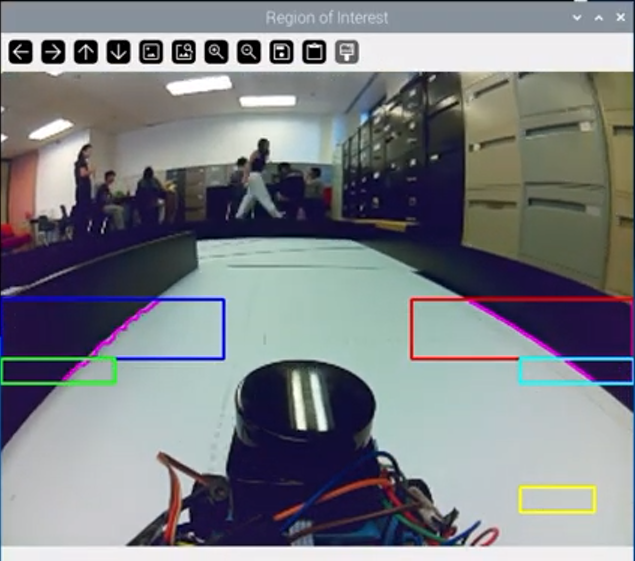
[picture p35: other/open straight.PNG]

  <br>
  <em>Open challenge ROIS</em>
</p>

##### Turning
The turning of the car is based on the threshold of the inside wall. Based on the direction of the track, we can deduce the inside wall. When the size of the wall reaches below a certain threshold, we start the turn by locking the steering angle until the number of pixels in the inside wall climbs back above the threshold. This allows us to adjust during turns, signalling to start a turn when we detect that a wall disappears, usually indicating when the inside wall ends.
```python
if left_area < WALL_THRESH:
  angle = TURN_ANGLE

elif right_area < WALL_THRESH:
  angle = -TURN_ANGLE
```
Past this initial turn, the rest of the turn relies on the angle calculating method in the straights.
##### Straights: Wall following with PID (Proportional-Integral-Derivative controller)

PID (Proportional-Integral-Derivative controller) is a feedback system that automatically adjusts and maintains a system's output to a desired setpoint. PID controllers analyze the difference between a setpoint and a measured process variable and use proportional, integral, and derivative terms to calculate a control output that keeps the system stable and accurate. In our case, we used PD (integral was not used) to center the car between the track walls for minimal oscillation.

Driving in the straights uses a PD calculating algorithm to find the angle the car should turn. This PD algorithm is comprised of proportional and derivative angle calculating, comprised of two constants: PD (proportional derivative) and PG (proportional gain).

First, we find the difference in the number of pixels of the wall and multiply it by the PD, and add the variation of the last two differences multiplied by the PD.

Proportion Gain decides the __direction__ of the car. If the left area is greater than the right, then the car must turn right at an angle. Proportional Derivative decides whether the change in angle is beneficial to the goal by comparing the current difference in wall size to the last difference in wall size. The PD essentially dampens PG's effect on the car's steering angle to prevent oscillation. We did not choose to use integral as we found that PG was enough to control oscillations. As a future improvement, PI may be added to further decrease instability

The final result is used as the angle and allows the car to adjust based on past feedback.

```python
curr_diff = right_area-left_area
angle = int((curr_diff * PG + (curr_diff-last_diff) * PD))
...
last_diff = curr_diff
```

As mentioned before, the change in track widths causes difficulties, particularly with this algorithm, as the wall difference becomes of higher magnitude due to the walls being larger as a whole (i.e., the ratio of wall size stays the same, but the difference in wall size increases due to the increase in wall size). Thus, the car became more sensitive to changes, leading to oscillations in narrow straights. To fix this issue, we lower the PD and PG when we detect a large number of pixels in both walls, as we now know we have entered a straight section.
```python
curr_diff = right_area-left_area
if right_area > 1250 and left_area > 1250:
  angle = int((curr_diff * PGLOW + (curr_diff-last_diff) * PDLOW))

else:
  angle = int((curr_diff * PG + (curr_diff-last_diff) * PD))

last_diff = curr_diff
```
This lower PD substantially reduces oscillation in the straights, making wall following more reliable and consistent.

##### Turn Counting
Turn counting is made simple by the lines on the track. When we detect the very first line, the colour of this line indicates the direction of the track. Starting from then, every time we see that first colour followed by the second colour, we add one to the turn count. 
First, we find the direction of the track from the first line.
```python
if track_dir == 0:

  if max_orange_area >= LINE_THRESH:
  track_dir = 1

elif max_blue_area >= LINE_THRESH:
  track_dir = -1
```
For all subsequent turns, we begin the turn by detecting the line we first saw on the track.
```python
if track_dir == 1:

  if max_orange_area >= LINE_THRESH:
  turning = True

elif track_dir == -1:

  if max_blue_area >= LINE_THRESH:
  turning = True
```
Lastly, we end the turn when we find the second line and add one to the turn count.
```python
if turning:

  if track_dir == 1:

    if max_blue_area >= LINE_THRESH:
        turning = False
        turn_count += 1

  if track_dir == -1:

    if max_orange_area >= LINE_THRESH:
        turning = False
        turn_count += 1
```
Rather than using one line to count turns, two lines are much more accurate and less prone to overcounting, as it doesn't allow overcounting where the car oscillates.

After 12 turns, we start incrementing a variable called `actions_to_straight`. After each loop, we increase the variable by one until it reaches a threshold. We then stop the code, allowing the car to end in the middle of the starting section rather than immediately after detecting the final line.
```python
if max_turns <= turn_count:
  actions_to_straight += 1

  if actions_to_straight >= 25:  
    board.pwm_servo_set_position(0.1, [[1, 1500]])
    board.pwm_servo_set_position(0.1, [[2, 1500]])
    break
```
<table>
  <tr>
    <td align="center" width="33%">
      <b>In a Straight Section</b><br>
      
    </td>
    <td align="center" width="33%">
      <b>Starting Turn</b><br>
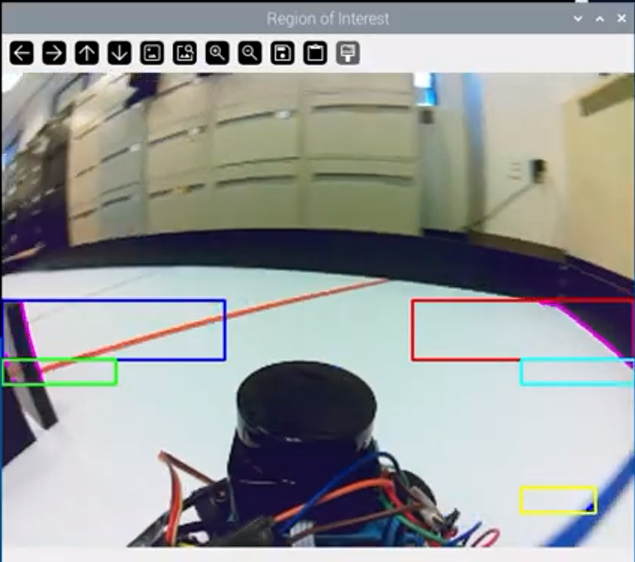
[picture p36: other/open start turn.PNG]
      
    </td>
    <td align="center" width="33%">
      <b>Ending Turn</b><br>
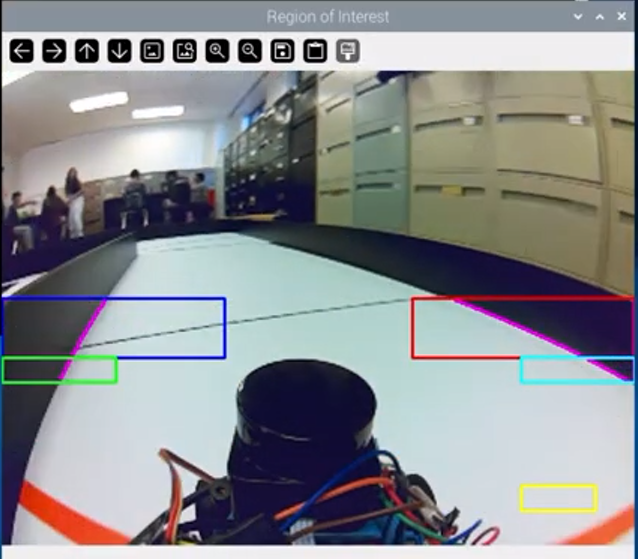
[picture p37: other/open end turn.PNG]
      
    </td>
  </tr>
</table>

<br>

### Obstacle Challenge
#### Overview of Challenge

The obstacle challenge is a more difficult version of the open challenge with the addition of traffic pillars and a parking lot.

In this challenge, the walls are set at (100 cm) and introduce red and green pillars that instruct the car on which side of the obstacle the car should pass. The car must pass red pillars on the right side and green pillars on the left side.

After 3 laps, the car must parallel park in the given parking space. The starting section, driving section and position of traffic signs are randomized. The parking lot is always in the starting section.

In addition, we may choose whether the car starts within the parking lot for an additional 7 points.
<p align="center">

  <br>
  <em> Obstacle Challenge Image</em>
</p>

#### Our Solution
We used the same four-wall ROIs and two-line detection ROIs. To check for pillars, we included one large ROI checking for both red and green pillars, covering most of the camera view. The top and bottom are partially be 
<p align="center">
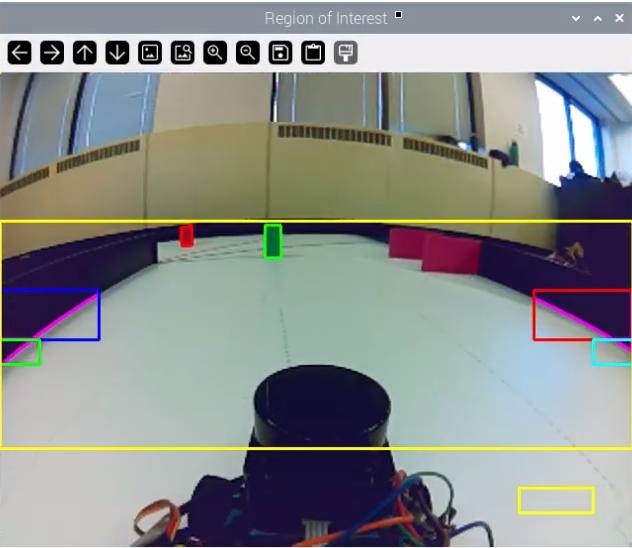
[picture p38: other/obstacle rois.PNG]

  <br>
  <em>ROIs in obstacle challenge</em>
</p>

We started by first attempting to follow the traffic signs in the correct direction in a straight section. To pass the pillar on the correct side, we set a target x coordinate on the camera for where we want the pillar to be when we pass it. For example, the red pillar's target is on the left side of the camera, ensuring that we pass the pillar on the right side when the pillar is at the target. For this, we use logic similar to the wall following PD algorithm in the open challenge, with a pillar PD and pillar PG. Instead of using the difference in the pixels of the wall to find the angle of the car turn, we find the error between the target and the centre x-coordinate of the pillar and multiply it by the pillar PG, then add the variation of the current and previous difference multiplied by the pillar PD. The pillar code takes priority over the wall following code from the open challenge. If there are no pillars in sight, we revert to the wall following algorithm.

```python
if selected_contour is not None:
  error = centre_pillar_x - target
  angle = -(int((error * PILLAR_PG) + ((error - last_pillar_diff) * PILLAR_PD)))
  last_diff = curr_diff
  last_pillar_diff= error

else:
  curr_diff = right_area-left_area
  angle = int((curr_diff * PG + (curr_diff-last_diff) * PD))
```
To smooth out the pillar targeting, we use dynamic gain instead of the pillar PD. This is calculated using the pillar PD, but it changes based on the distance to the pillar. If the pillar is further, the dynamic gain increases, and if the pillar is closer, the dynamic gain decreases.
```python
dynamic_gain = PILLAR_PG + (1 - normalized_y) * 0.0005
```
Even after tuning the pillar PG and PD, we still ran into an issue where our car would prioritise a pillar for too long, keeping the pillar in the target while running circles around it. To fix this issue, we created a variable called normalized_y, a ratio of how close the pillar is to the car. When the pillar approaches the car, the normalized_y increases, with a range between 0 and 1. This allowed us to set different targets based on the distance between the car and the pillar.
```python
if normalized_y < 0.2:
  RED_TARGET = 320
  GREEN_TARGET = 320

elif normalized_y < 0.4:
  RED_TARGET = 135
  GREEN_TARGET = 405

else:
  RED_TARGET = 75
  GREEN_TARGET = 565
# This is a simplified version of the targets.
```
However, due to a high PD and PG, the car would still follow the pillar in circles. To combat this problem, we ignore pillars in certain situations where they are close to the bottom camera and in the bottom left or right corners.
```python
if (centre_pillar_x  < 40 or centre_pillar_x > 600 ) and centre_pillar_y > 340:
  angle = 0
  print("ignoring pillar")
```
We also ignore the pillar following a lenient version of the condition above if the car had just finished a turn.
```python
if (centre_pillar_x  < 100 or centre_pillar_x > 540 ) and centre_pillar_y > 310 and (red_area2 < PILLAR_THRESH and green_area2 < PILLAR_THRESH) and not turning and time_after_turn >= 5:
  angle = 0
  print("ignoring pillar")
time_after_turn += 1
```
The original pillar algorithm works fine for most cases, unless the car sees a pillar in a different section above a wall. Since pillars take priority, the car attempts to get the pillar into the target, often running into a wall. We set a pillar threshold to fix this complication. We set a threshold for the pillars. Only pillars above a certain number of pixels will take priority, allowing us to only check pillars that are in the current section.
```python
if PILLAR_THRESH < cv2.contourArea(max_red_contour) > cv2.contourArea(max_green_contour):
  selected_contour = max_red_contour
  target = RED_TARGET

elif PILLAR_THRESH < cv2.contourArea(max_green_contour):
  selected_contour = max_green_contour
  target = GREEN_TARGET

else:
  selected_contour = None
```
Unfortunately, this didn't solve all our issues. Due to the random nature of the pillars, sometimes the pillars would be placed in a difficult case, where right after the turn, the pillar is set at a point that severely limits the amount of space the car has to turn. To fix these cases, we added a set angle for the car to turn at when it is within the orange and blue lines and doesn't see a pillar. This allows the car to turn earlier, seeing pillars and increasing the amount of time the car has to adjust its position.
```python
if turning:

  if track_dir==1:
    angle = -MAX_TURN_LESS

  else:
    angle = MAX_TURN_LESS
```
We also lower the pillar threshold during turns, allowing the car to straighten itself and predict the next pillars after a turn.
```python
if turning:

        PILLAR_THRESH = 150
        if track_dir == 1 and max_blue_area >= LINE_THRESH:
            turn_count += 1
            turning = False
            PILLAR_THRESH = 1200
            time_after_turn = 0

        elif track_dir == -1 and max_orange_area >= LINE_THRESH:
            turn_count += 1
            turning = False
            PILLAR_THRESH = 1200
            time_after_turn = 0
```
The turn-counting and wall following code is reused from the open challenge. To avoid the magenta parking lot, when we are not in a parking sequence, we count all magenta blocks as part of the wall, relying on the wall following algorithm to ignore the parking lot.

In short, we can use this flow chart to outline the overall process:
<p align="center">
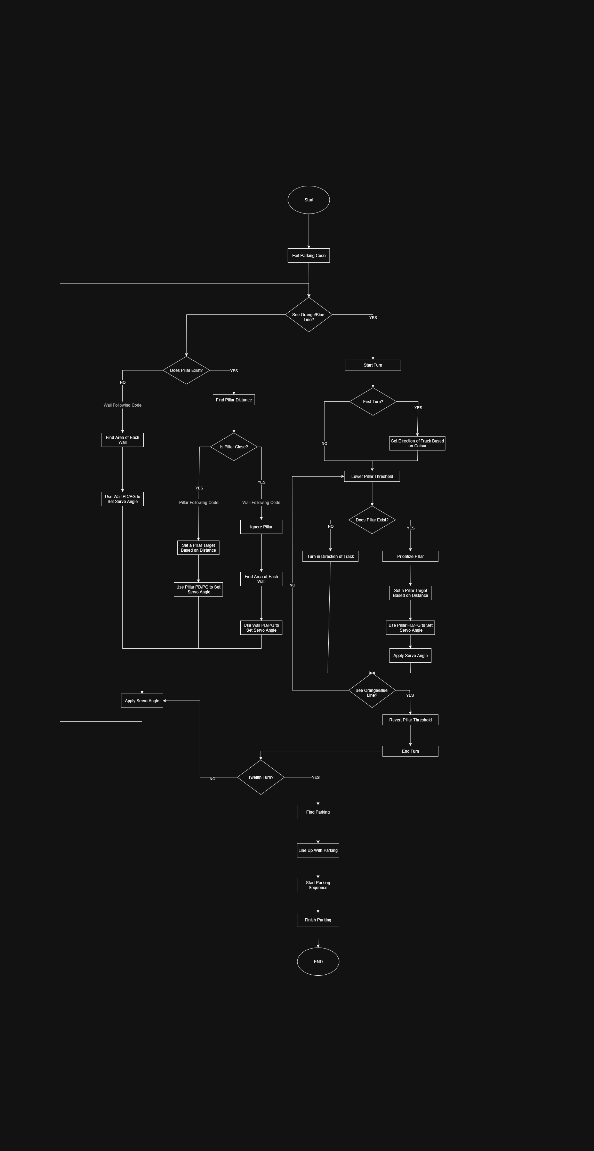
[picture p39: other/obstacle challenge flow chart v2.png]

  <br>
  <em>ROIs in obstacle challenge</em>
</p>
<br>

<table>
  <tr>
    <td align="center" width="33%">
      <b>Following Pillar</b><br>
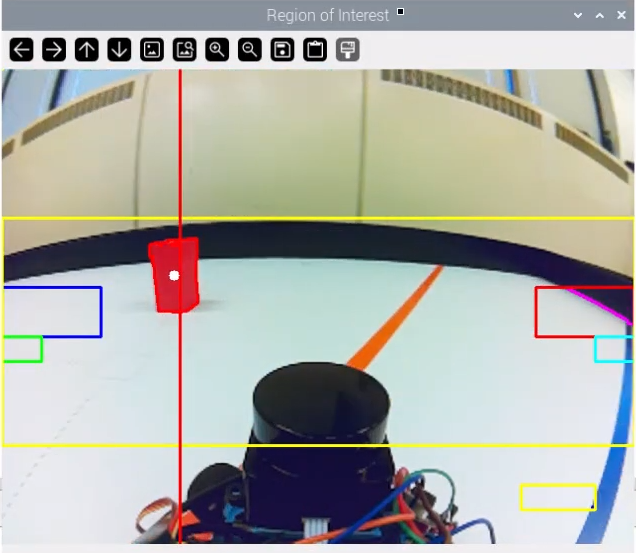
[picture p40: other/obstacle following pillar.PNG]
      
    </td>
    <td align="center" width="33%">
      <b>Ignoring Close Pillar</b><br>
      
    </td>
    <td align="center" width="33%">
      <b>Ignoring Far Pillar</b><br>
      
    </td>
  </tr>
</table>

#### Improvements
This challenge is perfect for the use of ROS2 due to its heavy computational requirements. ROIs allow you to run all processes in parallel and allows for easy sensor communication through the use of topics, publishers, subscribers, and other node types. At the beginning of this season, we did plan to use ROS2, but due to many reasons, we were not able to fully integrate it into the code. Unfortunately, be had to build ROS2 from source, which caused the workspace to be incredibly bulky and slow. As a side note to mention, the IMU sensor is still using an ROS2 node through threading. This is because using other methods has high latencies and causes a bottleneck. In the future, we wish to be able to fully make the switch over into ROS2 for optimal performance

## Parking
### Starting in Parking
We first check the direction of the car by checking the left and right distances on the lidar. 
```python
if left_distance < 300: # in mm
  direction = "left"
elif right_distance < 300:
  direction = "right"
else:
  direction = None
```
Fortunately, the turning radius of our car is high enough that we can turn out of parallel parking without any adjustments. This means this logic was a simple turn until the angle offset = 90 degrees
```python
starting_angle = get_imu_angle()

# turn out of parking
while True
  set_servo(MAX_TURN_DEGREE)
  set_motor(FORWARDS)
  angle_offset = get_imu_angle() - starting angle
  if angle_offset >= 90:
    break

# straighten car to original orientation
while True
  set_servo(-MAX_TURN_DEGREE)
  set_motor(FORWARDS)
  angle_offset = get_imu_angle() - starting angle
  if angle_offset <= 0:
    break
```

### Final Parallel Parking
Our approach for final parallel parking is similar to parallel parking as if you are driving a real car. However, to start this sequence, we must make sure we start in the same position every time.

To do this, we need to align the car at a certain angle every single time and be at the same distance every single time. To achieve this, we used the lidar distance from the wall PID and the imu to check the angle. This way, we always end in the same spot and at the same angle.
``` python
error = TARGET_DIST - right_distance
error_sum += error  # Just sum per iteration (integral)
d_error = error - last_error  # Difference per iteration (derivative)

pid_output = int(Kp * error + Ki * error_sum + Kd * d_error)
last_error = error

# Clamp steering angle
angle = max(-MAX_TURN_DEGREE, min(MAX_TURN_DEGREE, pid_output))
```
We can then parallel like regular, as follows, using Lidar and IMU to determine when to stop moving forward or backwards and when to stop turning <br>


<br>

## Assembly Instructions 🛠️
1. **Print the .stl files.**
- Using PLA filament, rearrange the components on the print bed in your slicer.
- The print may take upwards of 4 hours, so other steps can be done while this is happening.
  
2. **Organise the chassis parts.**
- From this chassis, we will need the motor mount, motor gear, bearings, differential gearbox, wheel axles, as well as the four wheels, all of which can be bought from the parts list.
- Any extra screws or electrical tape will be useful for miscellaneous parts.

3. **Combine the electrical components with the printed parts.**
- Place the differential gearbox into the rear, then secure it in place by attaching the `Furitek Micro Komodo Brushless Motor` to the motor mount using stock screws.
- Add the motor gear to mesh properly with the motor. (OPTIONAL: shorten the metal axle the gear is attached to; we chose not to.)
- The wheel axles can then be inserted into the metal bearings. Once fastened, attach the wheels using the nuts in the parts.
- Attach the `Hitec HS-5055MG Servo Motor` into the designated opening in the front chassis, again using stock screws.
- The rest of the 3D printed parts can then be attached from here with no interference, using the pictures of the 3d printed parts as a reference, or this video.
  

4. **Wire the system.**
- The `Furitek Micro Komodo Brushless Motor` can be directly wired to the `Furitek Micro Komodo ESC`
- The ESC can then be wired into the HAT, which has a specific port for 3-pronged motor wiring.
- The `Hitec HS-5055MG Servo Motor` can be wired similarly, but instead only using the one signal prong instead of all three.
  
- Then, the HAT is connected to the `Raspberry Pi 5` using a USB-C to USB-C, as well as a USB-C to USB-A
- Lastly, splice the wire of the battery and solder in an on/off switch.

5. **Final mounting.**
- Attach the Pi Camera onto the camera mount, then wire it into the CSI cable port on the `Raspberry Pi 5`.
- Place the `YDLidar T-mini` into the LIDAR mount, then wire it into the proper GPIO pins on the `Raspberry Pi 5`, according to the schematic in the schemes section.

6. **Software Configuration**
- Flash custom Raspberry Pi 5 Bookworm OS onto a micro SSD and insert it into the Raspberry Pi 5
- After powering on the PI, you will notice an Access Point (AP) pop up until the name `HW-<numbers & letters>`, connect using the password `hiwonder`
- Download RealVNC (link) and connect to `192.168.149.1`
- Open the terminal and switch the car into STA (wifi) mode:
	- ```cd hiwonder-toolbox \ sudo nano wifi_conf.py```
 	- `WIFI_MODE` to 2 instead of 1
  	- Replace the WiFi SSID and password with your current wifi network name and password
  	- `sudo reboot`
  	- Connect to your wifi and open _your_ computer's terminal
  	- Type `ipconfig` (Windows), `ifconfig` (Mac)
  	- Search your IPv4 address for your PI through any IP scanner; we used Advanced IP (link)
  	- Connect to this IP using RealVNC from the previous step
  	- Congrats! You now have a working mini-computer
 
- In the terminal, build ROS2-humble source using the following commands. ROS2 must be built from source, as this version of Linux does not support ROS2. This process may take upwards of 3 hours, so ensure your battery is fully charged.<br>
    i.
	```bashrc
 	sudo curl -sSL https://raw.githubusercontent.com/ros/rosdistro/master/ros.asc | sudo apt-key add -
	sudo sh -c 'echo "deb [arch=$(dpkg --print-architecture)] http://packages.ros.org/ros2/ubuntu
	$(lsb_release -cs) main" > /etc/apt/sources.list.d/ros2-latest.list'
	sudo apt update && sudo apt upgrade -y
	sudo apt install -y \
	build-essential cmake git wget curl gnupg lsb-release \
	libpython3-dev python3-colcon-common-extensions \
	python3-flake8 python3-pip python3-pytest-cov python3-rosdep \
	python3-setuptools python3-vcstool python3-numpy \
	libasio-dev libtinyxml2-dev libcunit1-dev unzip libyaml-dev
	sudo apt install -y libfastcdr-dev libfastrtps-dev
	sudo apt install -y python3-dev python3-numpy
	```
	2.
	```
 	sudo rosdep init || true
	rosdep update
 	```
 	3.
    ```
    mkdir -p ~/<WORKSPACE_NAME>/src
	cd ~/<WORKSPACE_NAME>
	wget https://raw.githubusercontent.com/ros2/ros2/humble/ros2.repos
	vcs import src < ros2.repos
    ```
    4.
    ```
    cd ~/<WORKSPACE_NAME>
	rosdep install --from-paths src --ignore-src -y --rosdistro humble \
	--skip-keys="fastcdr fastrtps rti-connext-dds-6.0.1 urdfdom_headers"
    ```
    5.
    ```
   	colcon build --symlink-install --packages-skip-regex '^rviz'
    ```
    6.
    ```
   	chsh -s /bin/bash
	sudo reboot
    ```
     7.
    ```
   	echo "source ~/fe_ws/install/setup.bash" << ~/.bashrc
	source ~/.bashrc
    ```

8. **Congratulations! You've built our robot!**
    - Try downloading all program files from `\src`, and run it yourself!
    	- Please make sure to download any dependencies for Python library. This includes:
			  - OpenCV (cv2)
			  - NumPy
     		- picamera2
       		- rclpy
         	- geometry_msgs
      - run `pip install <library>`   
    - Any other information can be found in this repository.

Thanks for reading!

## Youtube Videos
[Open Challenge Video](https://youtu.be/stK2e71D908) 

[Obstacle Challenge Video](https://youtu.be/-8iTvhqq1Cs)

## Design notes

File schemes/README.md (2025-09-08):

Electromechanical diagrams
====



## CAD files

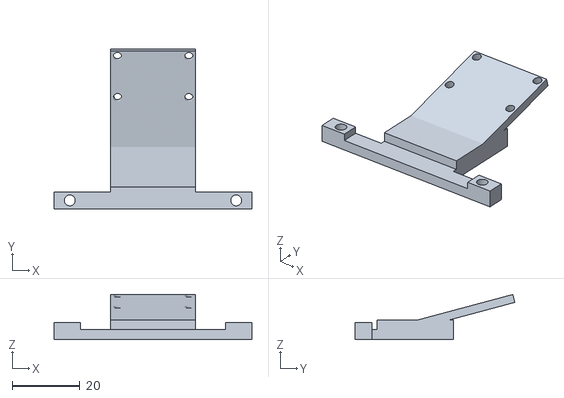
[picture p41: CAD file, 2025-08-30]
models/extra/camera holder v3.stl
58.3 x 47.1 x 13.3

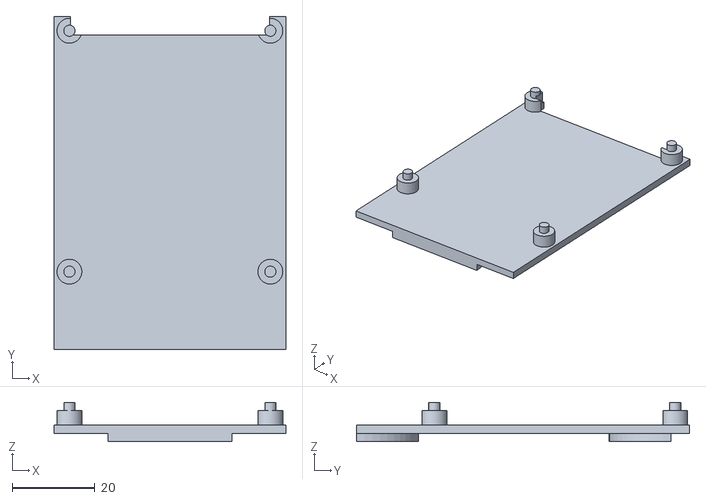
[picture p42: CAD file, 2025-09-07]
models/RPI Base.stl
56.0 x 80.5 x 9.50

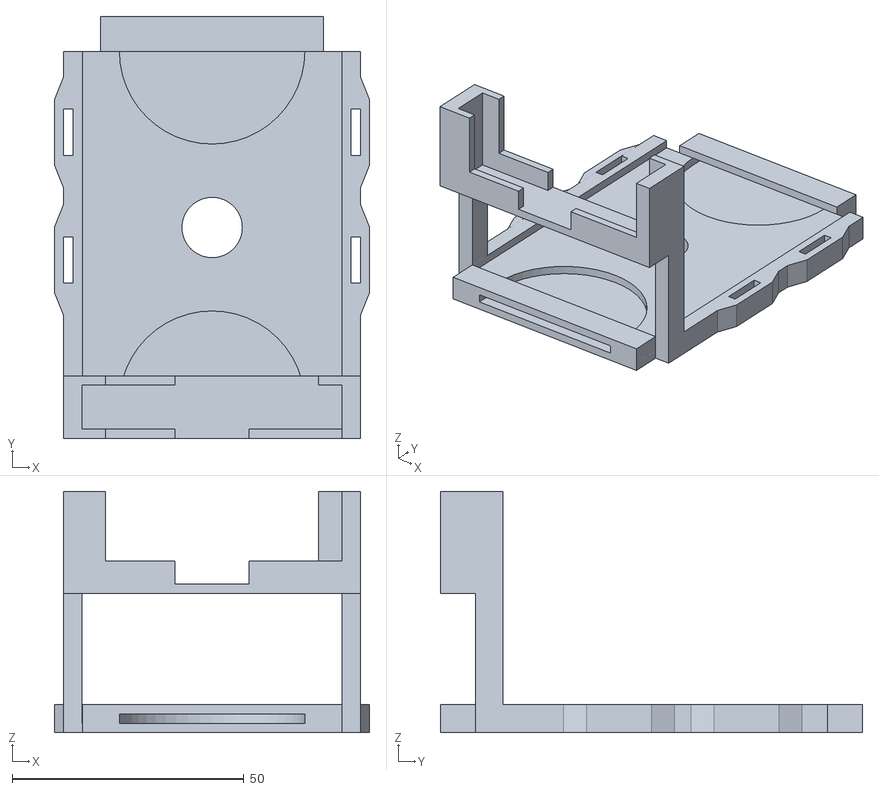
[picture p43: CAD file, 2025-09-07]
models/Base Plate.stl
68.0 x 91.0 x 52.0

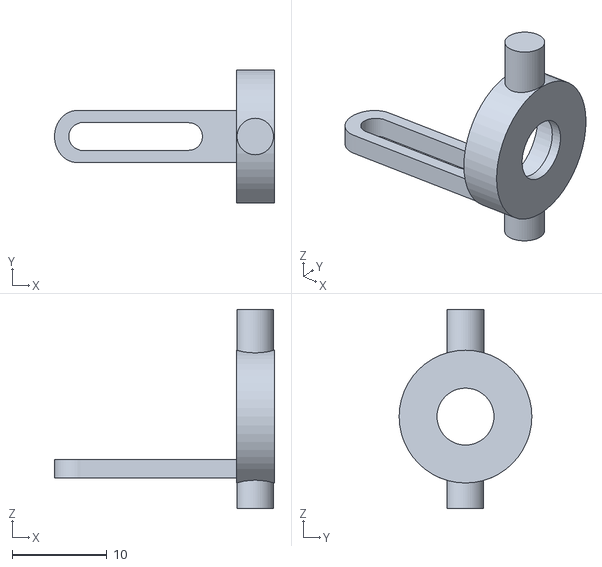
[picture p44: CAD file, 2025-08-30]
models/extra/Wheel Bearing Holder v6.stl
23.2 x 14.0 x 21.0

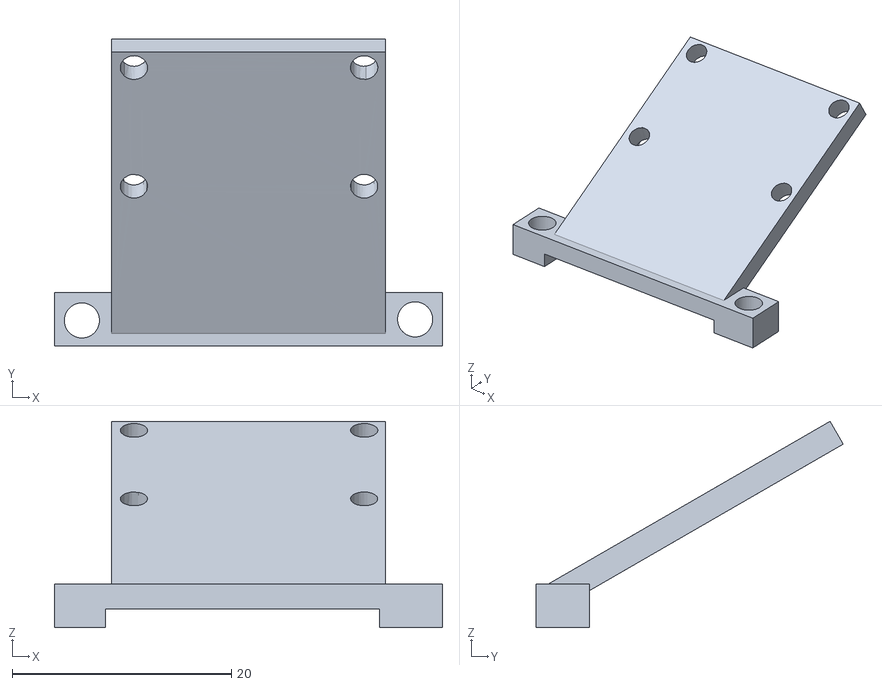
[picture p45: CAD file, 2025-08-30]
models/extra/camera stand v6 30deg adjustable.stl
35.4 x 28.1 x 18.8

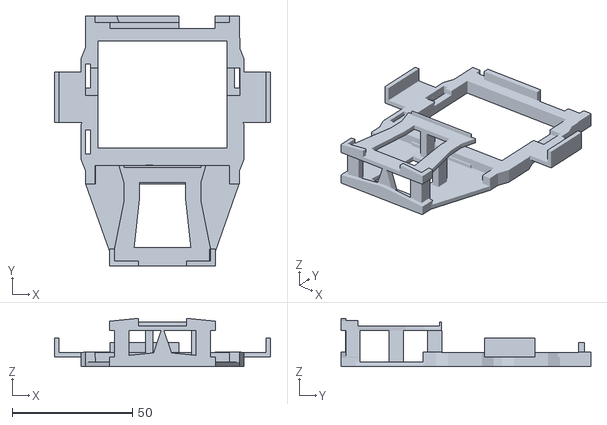
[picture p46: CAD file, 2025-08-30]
models/RSP HAT Holder v7.stl
90.0 x 104.0 x 20.1

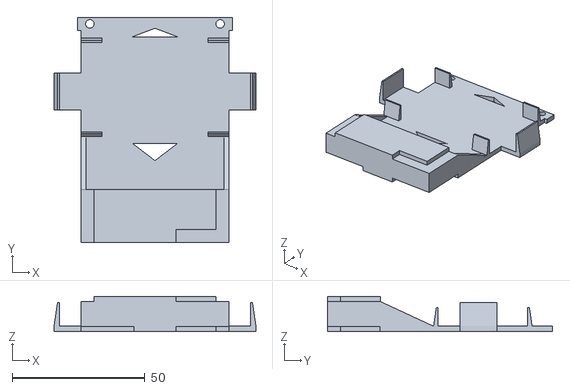
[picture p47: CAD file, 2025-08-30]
models/Battery and Camera Holder v4.stl
76.0 x 84.8 x 13.2

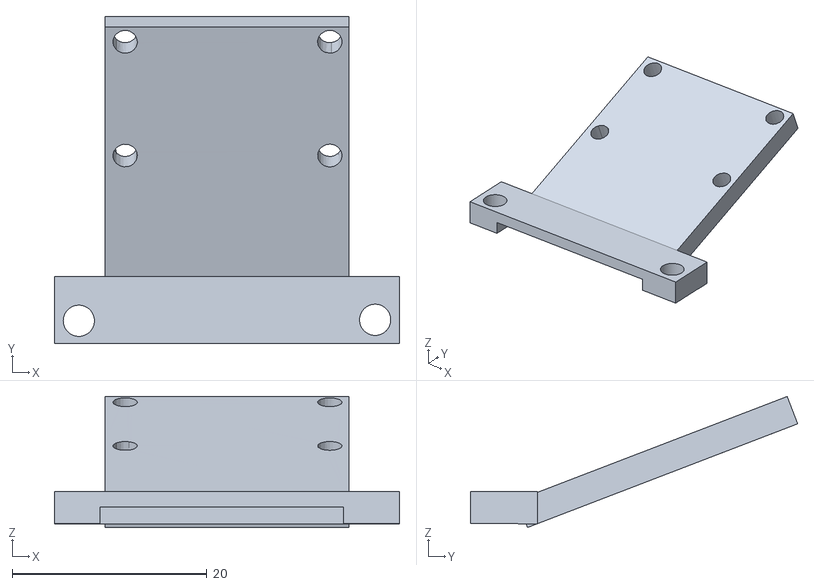
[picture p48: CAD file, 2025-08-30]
models/extra/camera stand v8 21deg adjustable.stl
35.4 x 33.6 x 13.4

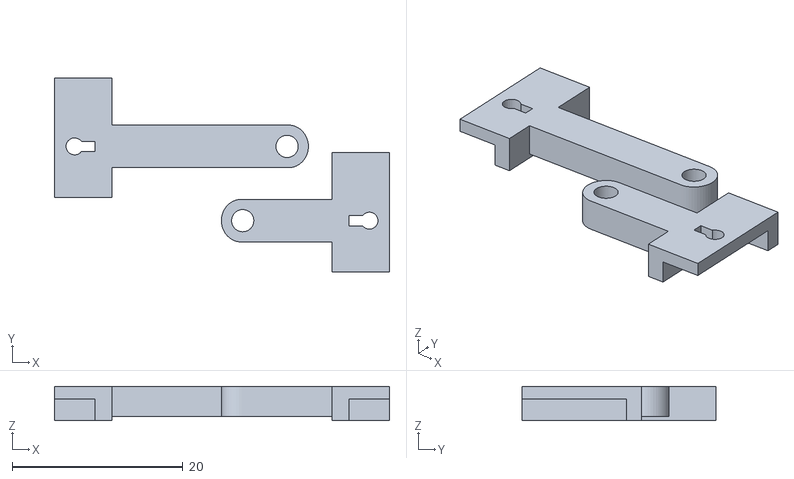
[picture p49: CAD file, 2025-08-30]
models/Axel Servo Holder.stl
39.2 x 22.7 x 4.00

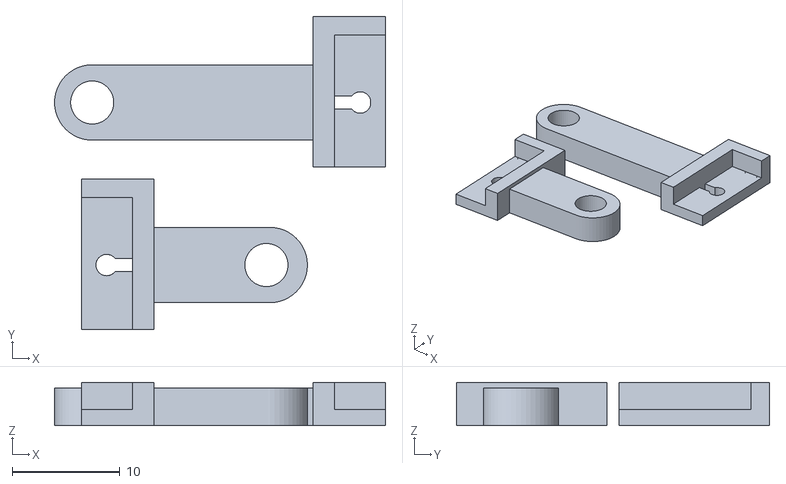
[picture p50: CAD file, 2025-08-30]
models/extra/Axel Servo Holder.stl
30.8 x 29.1 x 4.00

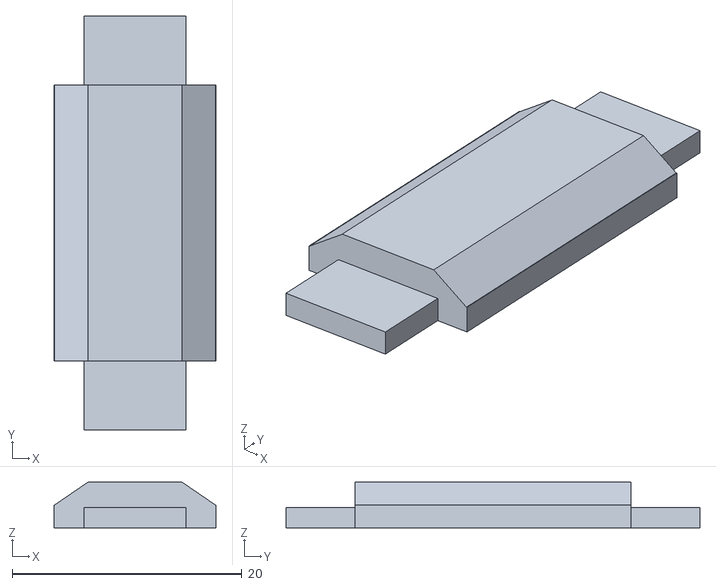
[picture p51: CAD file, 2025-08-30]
models/Chassis Pin v5.stl
14.1 x 36.0 x 4.00

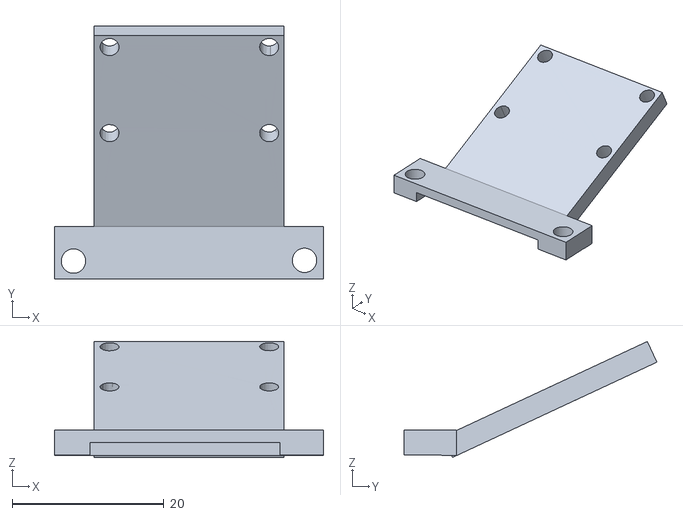
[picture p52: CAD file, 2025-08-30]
models/extra/camera stand v7 25deg adjustable.stl
35.4 x 33.3 x 15.3

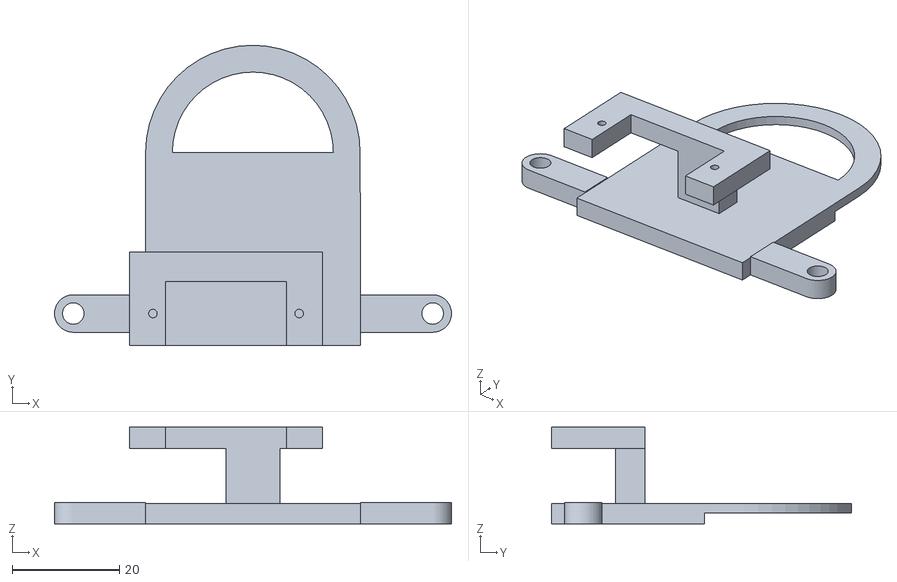
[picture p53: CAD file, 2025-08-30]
models/extra/Servo Stand v4.stl
74.0 x 56.0 x 18.0

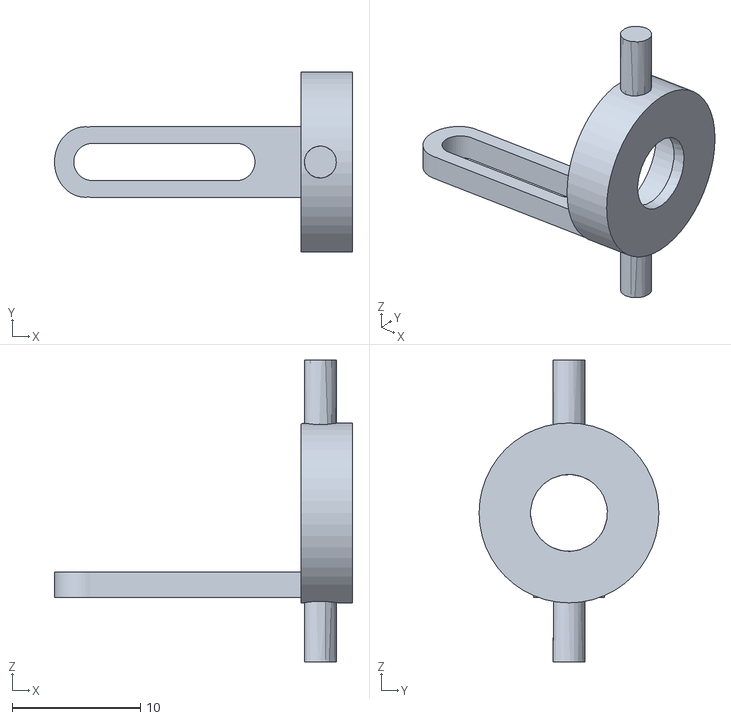
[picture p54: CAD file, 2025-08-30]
models/Wheel Bearing Holder v6.stl
23.2 x 14.0 x 23.5

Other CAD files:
models/Differential Cover v3.stl
models/extra/camera stand v5.stl
models/Camera Stand v9 25 deg.stl
models/extra/camera stand holder adjustable.stl
models/Front Axel v3.stl
models/Motor Gear Holder.stl
models/Rear Motor Stand v16.stl
models/Servo Stand v3.stl
models/Wheel Wrench.stl
models/extra/camera holder v2.stl

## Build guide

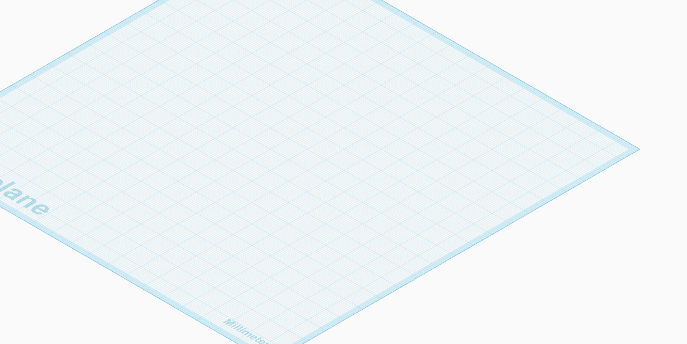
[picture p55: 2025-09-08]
other/model_images/assembly 19.png

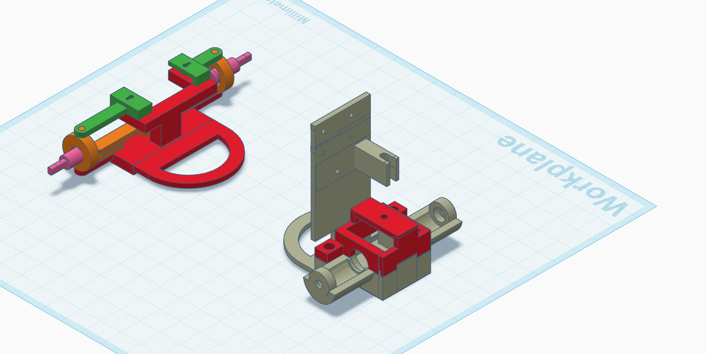
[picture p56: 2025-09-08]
other/model_images/assembly 10.png

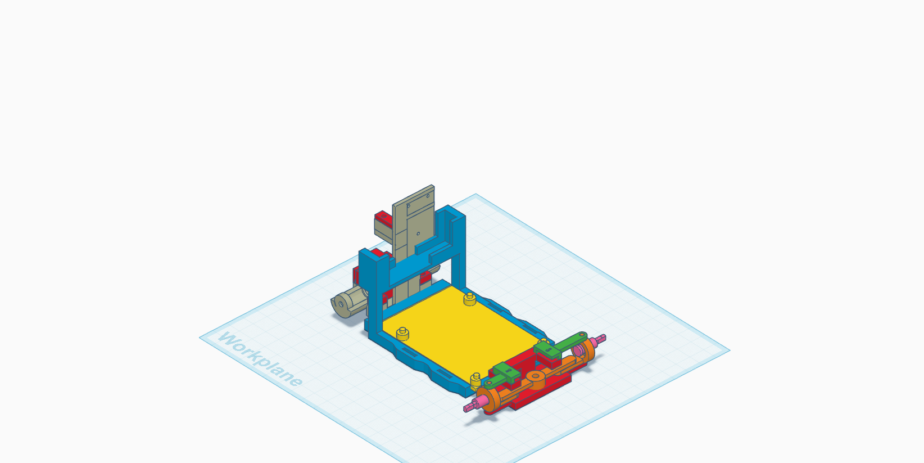
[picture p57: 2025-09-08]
other/model_images/assembly 6.png

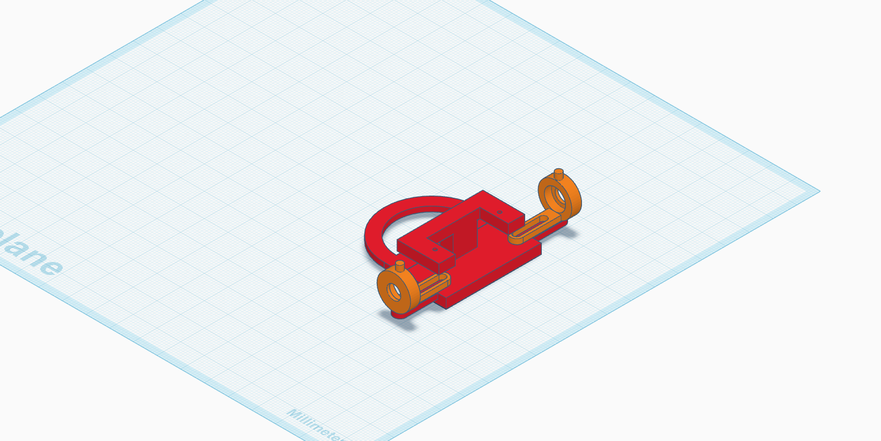
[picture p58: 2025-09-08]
other/model_images/assembly 16.png

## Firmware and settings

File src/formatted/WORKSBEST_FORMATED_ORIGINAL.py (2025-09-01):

import rclpy
import cv2
import numpy as np
from picamera2 import Picamera2
import threading
import ros_robot_controller_sdk as rcc
from helper import *
from CONSTS import *
#from exit_parking import unpark
import time
board = rcc.Board()

#red is right
#green is left

debug = False

speed = 1608
last_pil_diff = 0
last_diff = 0
turning = False
turn_dir = 0
track_dir = 0
curr_diff = 0
error = 0
angle = 0
turn_count = 0
time_after_turn = 0
target = 0

picam2 = Picamera2()
picam2.preview_configuration.main.size = (640,480)
picam2.preview_configuration.main.format = "RGB888"
print(picam2.preview_configuration.controls.FrameRate)
picam2.preview_configuration.controls.FrameRate = 75
picam2.set_controls({"Brightness": 0.05})
print(picam2.preview_configuration.controls.FrameRate)
picam2.preview_configuration.align()
picam2.configure("preview")
picam2.start()



while True:
    frame = picam2.capture_array()
    frame = cv2.resize(frame, (640, 480))
    
    if turn_count >= 12:
        board.pwm_servo_set_position(0.1, [[1, pwm(MID_SERVO)]])
        board.pwm_servo_set_position(0.1, [[2, 1500]])
        time.sleep(0.1)
        break


    img_lab = cv2.cvtColor(frame, cv2.COLOR_BGR2Lab)
    #img_lab = cv2.GaussianBlur(img_lab, (7, 7), 0)
    
    

    left_contours_top = findContours(img_lab, rBlack, ROI_LEFT_TOP)
    right_contours_top = findContours(img_lab, rBlack, ROI_RIGHT_TOP)
    left_contours_bot = findContours(img_lab, rBlack, ROI_LEFT_BOT)
    right_contours_bot = findContours(img_lab, rBlack, ROI_RIGHT_BOT)

    contours_blue1 = findContours(img_lab, rBlue, ROI_LINE1)

    contours_orange1 = findContours(img_lab, rOrange, ROI_LINE1)
    contours_blue2 = findContours(img_lab, rBlue, ROI_LINE2)

    contours_orange2 = findContours(img_lab, rOrange, ROI_LINE2)

    
    contours_red = findContours(img_lab, rRed, ROI_PILLAR)

    contours_green = findContours(img_lab, rGreen, ROI_PILLAR)
    
    for name, contours in [
    ("Left Top", left_contours_top),
    ("Right Top", right_contours_top),
    ("Left Bot", left_contours_bot),
    ("Right Bot", right_contours_bot),
    ("Blue1", contours_blue1),
    ("Orange1", contours_orange1),
    ("Blue2", contours_blue2),
    ("Orange2", contours_orange2),
    ("Red", contours_red),
    ("Green", contours_green),
]:
        if contours:
            areas = [cv2.contourArea(c) for c in contours]
            #print(f"{name} -> Count: {len(contours)}, Areas: {areas}")
            if "Blue" in name or "Orange" in name:
                #print("TURN INITISIUDIS DISDFHKJSFKJSDFKJDHSJDHJKDSBKJBDSBJFSFKJSFKJSKJBFJBSJKSJKFBKJSFBKSFBKJSFJKFBKFSKBFKJSBFKABSKSBKJSBJFBJSKJFKSBKJBSDKSBSFF")
                pass
        else:
            #print(f"{name} -> None")
            pass


    max_left_top_contour = sortContourShapes(left_contours_top)[0]
    left_area_top = cv2.contourArea(max_left_top_contour) if is_valid_contour(max_left_top_contour) else 0

    max_right_top_contour = sortContourShapes(right_contours_top)[0]
    right_area_top = cv2.contourArea(max_right_top_contour) if is_valid_contour(max_right_top_contour) else 0

    max_left_bot_contour = sortContourShapes(left_contours_bot)[0]
    left_area_bot = cv2.contourArea(max_left_bot_contour) if is_valid_contour(max_left_bot_contour) else 0

    max_right_bot_contour = sortContourShapes(right_contours_bot)[0]
    right_area_bot = cv2.contourArea(max_right_bot_contour) if is_valid_contour(max_right_bot_contour) else 0

    right_area = right_area_bot + right_area_top
    left_area = left_area_bot + left_area_top



    max_blue_contour1 = sortContourShapes(contours_blue1)[0] if contours_blue1 else None
    max_blue_area1 = cv2.contourArea(max_blue_contour1) if is_valid_contour(max_blue_contour1) else 0
    max_orange_contour1 = sortContourShapes(contours_orange1)[0] if contours_orange1 else None
    max_orange_area1 = cv2.contourArea(max_orange_contour1) if is_valid_contour(max_orange_contour1) else 0
    max_blue_contour2 = sortContourShapes(contours_blue2)[0] if contours_blue2 else None
    max_blue_area2 = cv2.contourArea(max_blue_contour2) if is_valid_contour(max_blue_contour2) else 0
    max_orange_contour2 = sortContourShapes(contours_orange2)[0] if contours_orange2 else None
    max_orange_area2 = cv2.contourArea(max_orange_contour2) if is_valid_contour(max_orange_contour2) else 0

    max_blue_area = max_blue_area2+max_blue_area1
    max_orange_area = max_orange_area2+max_orange_area1

    

    red_contours =  sortContourShapes(contours_red)
    max_red_contour = red_contours[0] if red_contours else None
    max_red_area = cv2.contourArea(max_red_contour) if is_valid_contour(max_red_contour) else 0

    green_contours = sortContourShapes(contours_green)
    max_green_contour = green_contours[0] if green_contours else None
    max_green_area = cv2.contourArea(max_green_contour) if is_valid_contour(max_green_contour) else 0

    red_contour2 = red_contours[1] if len(red_contours) > 1 else None
    red_area2 = cv2.contourArea(red_contour2) if is_valid_contour(red_contour2) else 0
    green_contour2 = green_contours[1] if len(green_contours) > 1 else None
    green_area2 = cv2.contourArea(green_contour2) if is_valid_contour(green_contour2) else 0


    if False:
        # Draw max orange contour (orange)
        drawContour(max_orange_contour1, ROI_LINE1, frame, color=(0, 165, 255), thickness=2)

        # Draw max blue contour (blue)
        drawContour(max_blue_contour1, ROI_LINE1, frame, color=(255, 0, 0), thickness=2)    

        drawContour(max_orange_contour2, ROI_LINE2, frame, color=(0, 165, 255), thickness=2)

        # Draw max blue contour (blue)
        drawContour(max_blue_contour2, ROI_LINE2, frame, color=(255, 0, 0), thickness=2)
    
        # Draw max black contours (magenta for visibility)
        drawContour(max_left_top_contour, ROI_LEFT_TOP, frame, color=(255, 0, 255), thickness=2)

        drawContour(max_right_top_contour, ROI_RIGHT_TOP, frame, color=(255, 0, 255), thickness=2)

        drawContour(max_left_bot_contour, ROI_LEFT_BOT, frame, color=(255, 0, 255), thickness=2)

        drawContour(max_right_bot_contour, ROI_RIGHT_BOT, frame, color=(255, 0, 255), thickness=2)

        drawContour(max_green_contour, ROI_PILLAR, frame, color=(0, 255, 0), thickness=2)

        drawContour(max_red_contour, ROI_PILLAR, frame, color=(0, 0, 255), thickness=2)

        # Draw all ROIs with logical color coding
        
        drawRect(ROI_LEFT_TOP, frame, color=(255, 0, 0), thickness=2)        # Blue - top left
        drawRect(ROI_RIGHT_TOP, frame, color=(0, 0, 255), thickness=2)       # Red - top right
        drawRect(ROI_LEFT_BOT, frame, color=(0, 255, 0), thickness=2)       # Green - bottom left
        drawRect(ROI_RIGHT_BOT, frame, color=(255, 255, 0), thickness=2)     # Cyan - bottom right
        drawRect(ROI_LINE1, frame, color=(0, 255, 255), thickness=2)     # Yellow - center/orientation line
        drawRect(ROI_LINE2, frame, color=(0, 255, 255), thickness=2)     # Yellow - center/orientation line
        drawRect(ROI_PILLAR, frame, color=(0, 255, 255), thickness=2)


    size = 0

    if is_valid_contour(max_red_contour) and is_valid_contour(max_green_contour):
        if PILLAR_THRESH < cv2.contourArea(max_red_contour) > cv2.contourArea(max_green_contour):
            selected_contour = max_red_contour
            target = RED_TARGET

            if debug:
                cv2.line(frame, (RED_TARGET, 0), (RED_TARGET, 480), (0, 0, 255), 2)
        elif PILLAR_THRESH < cv2.contourArea(max_green_contour):
            selected_contour = max_green_contour
            target = GREEN_TARGET
            if debug:
                cv2.line(frame, (GREEN_TARGET, 0), (GREEN_TARGET, 480), (0, 255, 0), 2)
        else:
            selected_contour = None

    elif is_valid_contour(max_red_contour) and PILLAR_THRESH < cv2.contourArea(max_red_contour):
        selected_contour = max_red_contour
        target = RED_TARGET
        cv2.line(frame, (RED_TARGET, 0), (RED_TARGET, 480), (0, 0, 255), 2)

    elif is_valid_contour(max_green_contour) and PILLAR_THRESH < cv2.contourArea(max_green_contour):
        selected_contour = max_green_contour
        target = GREEN_TARGET
        cv2.line(frame, (GREEN_TARGET, 0), (GREEN_TARGET, 480), (0, 255, 0), 2)

    else:
        selected_contour = None


    if is_valid_contour(selected_contour):
        last_diff = 0
        curr_diff = 0
        size = cv2.contourArea(selected_contour)
        x, y, w, h = cv2.boundingRect(selected_contour)
        cX = x + w // 2 #+ ROI_PILLAR[0]
        cY = (y + h // 2) #+ ROI_PILLAR[1]
        #cv2.rectangle(frame, (x, y), (x + w, y + h), (0, 255, 0), 2)

        # Normalize y-distance
        pillar_roi_bottom = ROI_PILLAR[3]
        pillar_roi_top = ROI_PILLAR[1]
        normalized_y = (cY - pillar_roi_top) / (pillar_roi_bottom - pillar_roi_top)
        normalized_y = np.clip(normalized_y, 0.0, 1.0)

        # Dynamic gain
        dynamic_gain = PILLAR_PG + (1 - normalized_y) * 0.0005

        if normalized_y < 0.2:
            RED_TARGET = 320
            GREEN_TARGET = 320
        elif normalized_y < 0.35:
            RED_TARGET = 180
            GREEN_TARGET = 460
        elif normalized_y < 0.4:
            RED_TARGET = 135
            GREEN_TARGET = 405
        elif normalized_y < 0.45:
            RED_TARGET = 90
            GREEN_TARGET = 550
        else:
            RED_TARGET = 75
            GREEN_TARGET = 565
        
        
        error = cX-target
        
        angle = -(int((error * dynamic_gain) + ((error - last_pil_diff) * PILLAR_PD)))#*(normalized_y+1))#*(normalized_y/2+0.5)))
        
        
        print("target:", target, "left area:", left_area, "right area", right_area, "track_dir:", track_dir)

        if (cX  < 40 or cX > 600 ) and cY > 340:
            angle = 0
            print("ignoring pillar")
            print(cX, cY)
        if (cX  < 100 or cX > 540 ) and cY > 310 and (red_area2 < PILLAR_THRESH and green_area2 < PILLAR_THRESH) and not turning and time_after_turn >= 5:
            angle = 0
            print("ignoring pillar EBCAUSW IR SAEEES NO NEXT")
            print(cX, cY)

        cv2.circle(frame, (cX, cY), 5, (255, 255, 255), -1)
        print("normalized_y: ", normalized_y)


    else:
        curr_diff = right_area - left_area
        angle = int((curr_diff * PG + (curr_diff-last_diff) * PD))
        print("using wallsISNDSNKSDNSJSJDJSJJSDJSD", angle)
        print(curr_diff, last_diff, curr_diff-last_diff)

        if turning:
            if track_dir==1:

                angle = -MAX_TURN_LESS
            else:
                angle = MAX_TURN_LESS

    if turning:
        print("TURFNDINFJDBNFDNNFDDJNFFNFE")
        PILLAR_THRESH = 150
        if track_dir == 1 and max_blue_area >= LINE_THRESH:
            turn_count += 1
            turning = False
            PILLAR_THRESH = 1200
            time_after_turn = 0
            print("TURN ENDED")
        elif track_dir == -1 and max_orange_area >= LINE_THRESH:
            turn_count += 1
            turning = False
            PILLAR_THRESH = 1200
            print("TURNENEDEDED")
            time_after_turn = 0

    elif track_dir == 0:
        if max_orange_area >= LINE_THRESH:
            track_dir = 1
            ROI_LINE1 = [0,0,0,0]
            ROI_LINE2 = [40,420,115,445]
        elif max_blue_area >= LINE_THRESH:
            track_dir = -1
            ROI_LINE2 = [0,0,0,0]
            ROI_LINE1 = [525,420,600,445]

    elif track_dir == 1:
        if max_orange_area >= LINE_THRESH:
            turning = True

        elif max_blue_area >= LINE_THRESH:
            pass

    elif track_dir == -1:
        if max_orange_area >= LINE_THRESH:
            pass
        elif max_blue_area >= LINE_THRESH:
            turning = True

    time_after_turn += 1
    if debug:
        cv2.imshow("Region of Interest", frame)
    cv2.waitKey(1)

    print(angle, "turn: ", turn_count)

    if angle>40:
        angle=40
    elif angle<-40:
        angle=-40

    servo = angle
    print(angle,speed)
    dc = speed
    board.pwm_servo_set_position(0.1, [[1, pwm(angle+MID_SERVO)]])
    board.pwm_servo_set_position(0.1, [[2, dc]])

    last_diff = curr_diff
    last_pill_diff= error



import rclpy
import cv2
import numpy as np
from picamera2 import Picamera2
from gpiozero import DigitalOutputDevice
import ros_robot_controller_sdk as rcc
from helper import *
from CONSTS import *
from lidar_parser import *
import math
from imu import *  # start_imu_stream, read_imu_line, stop_imu_stream
import time
import serial

board = rcc.Board()
lidar_power = DigitalOutputDevice(LIDAR_POWER_PIN)
lidar_power.on()
time.sleep(1)
print("LD19 powered ON via GPIO 17.")

latest_points = {}  
debug = True
speed = 1605
last_pil_diff = 0
last_diff = 0
turning = False
turn_dir = 0
track_dir = 0
curr_diff = 0
error = 0
angle = 0
turn_count = 0
time_after_turn = 0
target = 0
CONF_THRESHOLD = 0

def store_latest_points(parsed):
    angles = interpolate_angles(parsed["start_angle"], parsed["end_angle"], len(parsed["points"]))
    ts = parsed["timestamp"]
    for (dist, conf), angle in zip(parsed["points"], angles):
        angle_key = int(round(angle)) % 360
        if conf >= CONF_THRESHOLD:
            latest_points[angle_key] = (dist, conf, ts)
        else:
            if angle_key not in latest_points:
                latest_points[angle_key] = (dist, conf, ts)

def get_latest_distance(angle_query, tolerance=2):
    angle_key = int(round(angle_query)) % 360
    if angle_key in latest_points:
        dist, conf, ts = latest_points[angle_key]
        return {"distance": dist, "confidence": conf, "angle": angle_key, "timestamp": ts}
    candidates = [
        (abs(k - angle_key), k, latest_points[k])
        for k in latest_points
        if abs((k - angle_key + 180) % 360 - 180) <= tolerance
    ]
    if not candidates:
        return None
    _, k, (dist, conf, ts) = min(candidates, key=lambda x: x[0])
    return {"distance": dist, "confidence": conf, "angle": k, "timestamp": ts}

def set_motion(direction):
    if direction == "forward":
        board.pwm_servo_set_position(0.1, [[2, 1500]])  # 1590
    elif direction == "reverse":
        board.pwm_servo_set_position(0.1, [[2, 1500]])  # 1390

def stop_motion():
    board.pwm_servo_set_position(0.1, [[1, pwm(MID_SERVO)]])
    board.pwm_servo_set_position(0.1, [[2, 1500]])

def set_steering(position):
    if position == "left":
        board.pwm_servo_set_position(0.1, [[1, pwm(MID_SERVO - MAX_TURN_DEGREE)]])
    elif position == "right":
        board.pwm_servo_set_position(0.1, [[1, pwm(MID_SERVO)]])
    elif position == "straight":
        board.pwm_servo_set_position(0.1, [[1, pwm(MID_SERVO)]])

track_dir = 1
LED(board, (0, 255, 0))

if track_dir != 0:
    ser = serial.Serial(PORT, BAUD, timeout=0.1)
    buffer = bytearray()
    imu_proc = start_imu_stream()
    print(imu_proc)

    in_vector_block = False
    last_yaw_rad = None
    initial_yaw_rad = None
    state = "detect_wall"
    wall_side = None
    dist_from_front = 0
    offset_deg = 0

    print("starting reading")
    time.sleep(1)

    def unsigned_circular_diff_rad(a_rad, b_rad):
        d = a_rad - b_rad
        d = (d + math.pi) % (2.0 * math.pi) - math.pi
        return abs(d)

    try:
        while True:
            data = ser.read(256)
            if data:
                buffer += data
                while True:
                    idx = find_packet_start(buffer)
                    if idx == -1 or len(buffer) - idx < PACKET_LEN:
                        break
                    packet = buffer[idx:idx + PACKET_LEN]
                    buffer = buffer[idx + PACKET_LEN:]
                    parsed = parse_packet(packet)
                    if parsed:
                        store_latest_points(parsed)

            front = get_latest_distance(270.0)
            left = get_latest_distance(180.0)
            right = get_latest_distance(0.0)

            line = read_imu_line(imu_proc)

            if line:
                if line.startswith("vector:"):
                    in_vector_block = True
                elif in_vector_block and line.startswith("z:"):
                    try:
                        z_rad = float(line.split(":", 1)[1].strip())
                        if z_rad < 0:
                            z_rad += (2 * math.pi)
                        last_yaw_rad = z_rad
                        if initial_yaw_rad is None:
                            initial_yaw_rad = z_rad
                    except ValueError:
                        pass
                    in_vector_block = False

            if last_yaw_rad and initial_yaw_rad:
                offset_rad = unsigned_circular_diff_rad(last_yaw_rad, initial_yaw_rad)
                offset_deg = math.degrees(offset_rad)
            print(f"Offset: {offset_deg:.2f} deg | Yaw: {math.degrees(last_yaw_rad):.2f} deg")

            if front and left and right:
                if state == "detect_wall":
                    if left and right:
                        if left["distance"] < 500:
                            wall_side = "left"
                            state = "front_turn"
                        elif right["distance"] < 500:
                            wall_side = "right"
                            state = "front_turn"

                    if front:
                        dist_from_front = front["distance"]

                elif state == "front_turn":
                    set_steering(wall_side)
                    set_motion("forward")
                    if (front and front["distance"] < 50) or (right and right["distance"] < 50) or (left and left["distance"] < 50):
                        stop_motion()
                        time.sleep(2)
                        state = "reverse_turn"

                elif state == "reverse_turn":
                    set_steering(["left", "right"][wall_side == "left"])
                    set_motion("reverse")
                    if offset_deg > 40:
                        stop_motion()
                        state = "turn_til_90"

                elif state == "turn_til_90":
                    set_steering(wall_side)
                    set_motion("forward")
                    if offset_deg > 0:
                        stop_motion()
                        break

    except KeyboardInterrupt:
        pass
    finally:
        stop_imu_stream(imu_proc)
        ser.close()
        lidar_power.off()
        time.sleep(1)

LED(board, (0, 0, 0))

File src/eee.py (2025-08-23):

import rclpy
import cv2
import numpy as np
from picamera2 import Picamera2
import ros_robot_controller_sdk as rcc
import time
board = rcc.Board()

#red is right
#green is left

def pwm(degree):  
    pw = round(degree * 11.1 + 1500)
    return max(0, min(65535, pw))

LOWER_BLACK_THRESHOLD = np.array([0, 0, 0])
UPPER_BLACK_THRESHOLD = np.array([180, 255, 83])

LOWER_BLUE = np.array([91, 115, 103])
UPPER_BLUE = np.array([132, 255, 255])

LOWER_ORANGE1 = np.array([0, 101, 173])
UPPER_ORANGE1 = np.array([27, 255, 255])
LOWER_ORANGE2 = np.array([0, 0, 0])
UPPER_ORANGE2 = np.array([0, 0, 0])

LOWER_RED_THRESHOLD1 = np.array([0, 120, 138])
UPPER_RED_THRESHOLD1 = np.array([8, 255, 255])
LOWER_RED_THRESHOLD2 = np.array([163, 120, 138]) 
UPPER_RED_THRESHOLD2 = np.array([180, 255, 255]) 

LOWER_GREEN_THRESHOLD = np.array([71, 82, 75])
UPPER_GREEN_THRESHOLD = np.array([100, 255, 178])

LOWER_MAGENTA_THRESHOLD1 = np.array([0, 0, 0])
UPPER_MAGENTA_THRESHOLD1 = np.array([0, 0, 0])
LOWER_MAGENTA_THRESHOLD2 = np.array([137, 168, 173])
UPPER_MAGENTA_THRESHOLD2 = np.array([162, 255, 255])


ROI_LEFT_TOP = [0, 220, 100, 270]        
ROI_RIGHT_TOP = [540, 220, 640, 270]
ROI_LEFT_BOT = [0, 270, 40, 295]
ROI_RIGHT_BOT = [600, 270, 640, 295]
# ROI_LEFT_TOP = [0, 220, 225, 270]        
# ROI_RIGHT_TOP = [415, 240, 640, 290]
# ROI_LEFT_BOT = [0, 270, 115, 295]
# ROI_RIGHT_BOT = [525, 290, 640, 315]

ROI_LINE1 = [525,400,600,425]
ROI_LINE2 = [40,400,115,425]
ROI_PILLAR = [0,140,640,380]
RED_TARGET = 110
GREEN_TARGET = 530

PD = 0.00004
PG = 0.0045
# PILLAR_PD = 0.00003
# PILLAR_PG = 0.00002
#PD = 0.000000002
#PG = 0.00000003
PDLOW = 0.00001
PGLOW = 0.0015
min_size=100000
#PILLAR_PD = 0.005
PILLAR_PD = 0.3
PILLAR_PG = 0.05
LINE_THRESH = 120
WALL_THRESH = 20
MAX_TURN_DEGREE = 40
PILLAR_THRESH = 1200
MID_SERVO = -6
speed = 1608
last_pil_diff = 0
last_diff = 0
turning = False
turn_dir = 0
track_dir = 0
curr_diff = 0
error = 0
angle = 0
turn_count = 0


debug = True

def findMaxContourShape(contours):
    if contours is None:
        raise Exception
    max_area = 0
    max_contour = None
    for cnt in contours:
        area = cv2.contourArea(cnt)
        if area > max_area:
            max_area = area
            max_contour = cnt
    return max_contour, max_area

def is_valid_contour(c):
    return c is not None and isinstance(c, (list, tuple, np.ndarray)) and len(c) > 0


picam2 = Picamera2()
picam2.preview_configuration.main.size = (640,480)
picam2.preview_configuration.main.format = "RGB888"
print(picam2.preview_configuration.controls.FrameRate)
picam2.preview_configuration.controls.FrameRate = 75
picam2.set_controls({"Brightness": 0.05})
print(picam2.preview_configuration.controls.FrameRate)
picam2.preview_configuration.align()
picam2.configure("preview")
picam2.start()



while True:
    frame = picam2.capture_array()
    frame = cv2.resize(frame, (640, 480))
    
    if turn_count >= 12:
        board.pwm_servo_set_position(0.1, [[1, pwm(MID_SERVO)]])
        board.pwm_servo_set_position(0.1, [[2, 1500]])
        time.sleep(0.1)
        break


    img_hsv = cv2.cvtColor(frame, cv2.COLOR_BGR2HSV)

    img_thresh = cv2.inRange(img_hsv, LOWER_BLACK_THRESHOLD, UPPER_BLACK_THRESHOLD)
    b_mask = cv2.inRange(img_hsv, LOWER_BLUE, UPPER_BLUE)
    o_mask = cv2.bitwise_or(
        cv2.inRange(img_hsv, LOWER_ORANGE1, UPPER_ORANGE1),
        cv2.inRange(img_hsv, LOWER_ORANGE2, UPPER_ORANGE2),
    )
    r_mask = cv2.bitwise_or(
            cv2.inRange(img_hsv, LOWER_RED_THRESHOLD1, UPPER_RED_THRESHOLD1),
            cv2.inRange(img_hsv, LOWER_RED_THRESHOLD2, UPPER_RED_THRESHOLD2),
        )
    g_mask = cv2.inRange(img_hsv, LOWER_GREEN_THRESHOLD, UPPER_GREEN_THRESHOLD)

    left_contours_top, hierarchy = cv2.findContours(
        img_thresh[
            ROI_LEFT_TOP[1] : ROI_LEFT_TOP[3], ROI_LEFT_TOP[0] : ROI_LEFT_TOP[2]
        ],
        cv2.RETR_EXTERNAL,
        cv2.CHAIN_APPROX_NONE,
    )
    right_contours_top, hierarchy = cv2.findContours(
        img_thresh[
            ROI_RIGHT_TOP[1] : ROI_RIGHT_TOP[3], ROI_RIGHT_TOP[0] : ROI_RIGHT_TOP[2]
        ],
        cv2.RETR_EXTERNAL,
        cv2.CHAIN_APPROX_NONE,
    )
    left_contours_bot, hierarchy = cv2.findContours(
        img_thresh[
            ROI_LEFT_BOT[1] : ROI_LEFT_BOT[3], ROI_LEFT_BOT[0] : ROI_LEFT_BOT[2]
        ],
        cv2.RETR_EXTERNAL,
        cv2.CHAIN_APPROX_NONE,
    )
    right_contours_bot, hierarchy = cv2.findContours(
        img_thresh[
            ROI_RIGHT_BOT[1] : ROI_RIGHT_BOT[3], ROI_RIGHT_BOT[0] : ROI_RIGHT_BOT[2]
        ],
        cv2.RETR_EXTERNAL,
        cv2.CHAIN_APPROX_NONE,
    )

    contours_blue1 = cv2.findContours(
        b_mask[ROI_LINE1[1] : ROI_LINE1[3], ROI_LINE1[0] : ROI_LINE1[2]],
        cv2.RETR_EXTERNAL,
        cv2.CHAIN_APPROX_SIMPLE,
    )[-2]

    contours_orange1 = cv2.findContours(
        o_mask[ROI_LINE1[1] : ROI_LINE1[3], ROI_LINE1[0] : ROI_LINE1[2]],
        cv2.RETR_EXTERNAL,
        cv2.CHAIN_APPROX_SIMPLE,
    )[-2]

    contours_blue2 = cv2.findContours(
        b_mask[ROI_LINE2[1] : ROI_LINE2[3], ROI_LINE2[0] : ROI_LINE2[2]],
        cv2.RETR_EXTERNAL,
        cv2.CHAIN_APPROX_SIMPLE,
    )[-2]

    contours_orange2 = cv2.findContours(
        o_mask[ROI_LINE2[1] : ROI_LINE2[3], ROI_LINE2[0] : ROI_LINE2[2]],
        cv2.RETR_EXTERNAL,
        cv2.CHAIN_APPROX_SIMPLE,
    )[-2]

    
    contours_red = cv2.findContours(
            r_mask[ROI_PILLAR[1] : ROI_PILLAR[3], ROI_PILLAR[0] : ROI_PILLAR[2]],
            cv2.RETR_EXTERNAL,
            cv2.CHAIN_APPROX_SIMPLE,
        )[-2]

    contours_green = cv2.findContours(
        g_mask[ROI_PILLAR[1] : ROI_PILLAR[3], ROI_PILLAR[0] : ROI_PILLAR[2]],
        cv2.RETR_EXTERNAL,
        cv2.CHAIN_APPROX_SIMPLE,
    )[-2]
    
    contours_green = cv2.findContours(
        g_mask[ROI_PILLAR[1] : ROI_PILLAR[3], ROI_PILLAR[0] : ROI_PILLAR[2]],
        cv2.RETR_EXTERNAL,
        cv2.CHAIN_APPROX_SIMPLE,
    )[-2]

    max_left_top_contour, left_area_top = findMaxContourShape(left_contours_top)
    max_right_top_contour, right_area_top = findMaxContourShape(right_contours_top)
    max_left_bot_contour, left_area_bot = findMaxContourShape(left_contours_bot)
    max_right_bot_contour, right_area_bot = findMaxContourShape(right_contours_bot)
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

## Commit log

2025-06-05 imu peusdo
2025-06-05 camera and button start pesufo
2025-06-08 Rename wro thing (7).stl to Differential drive axel.stl
    [Differential drive axel.stl]
2025-06-08 Rename Differential drive axel.stl to differential drive axel.stl
    [differential drive axel.stl]
2025-06-23 Rename full chassis v1.stl to chassis v2.stl
    [chassis v2.stl]
2025-07-05 Rename schemes/Schematic_wrofuture-copy_2025-07-05.png to WRO 2025 Schematic (No Lidar).png
2025-07-05 camera settings and hsv ranges
2025-07-05 led node
2025-07-06 Rename Schematic_wrofuture-copy_2025-07-05 (1).png to Schematic WRO FE 2025.png
2025-07-06 led node updates
2025-07-06 led_node works
2025-07-06 better led colour setting
2025-07-06 leds in navigate
2025-07-06 bug fixes after running
    [navigateopen.py]
2025-07-06 bugss fixed when running
    [navigateopen.py]
2025-07-06 bug fixes when tesgting
    [control.py, navigateopen.py]
2025-07-06 Update README.md
    add power draw table
2025-07-06 gyro test sucess and wallfollowing test base
2025-07-06 manual control, pid testing runs
2025-07-12 max turn degree and servo mid degree
    changed due to servo attatchment redesigning
    [cameraopen.py, control.py, navigateopen.py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]
2025-08-26 format code and add lidar and imu code
2025-08-29 lab works i think probably idk bruv the car broke but it runs
    [CONSTS.py, beginningparking.py, helper.py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]
2025-08-30 fixed offset issues, debug mode off now works
    [WORKSBEST_FORMATED_ORIGINAL.py, beginningparking.py, helper.py]
2025-08-30 updated mechanical breakdown section. added a place to show images of individual parts and car, as well as a brief overview of material and design choices.
2025-08-31 additional information to mechanical section
    added material pros and cons.
    added place holder images
    additional information on design choices
2025-08-31 added the chassis section to mobility management
2025-08-31 Update README.md
    added parts and fixed lidar link and name
2025-08-31 Rename Schematic_wrofuture-copy_2025-08-31.png to Schematic WRO FE 2025.png
2025-08-31 added camera section in chassis
2025-08-31 reediting camera
2025-08-31 extended printed parts table
2025-08-31 changed plate table to html
2025-09-01 fixed open, turn method w/ wall thresh
    [OOOOOOOOP.py, beginningparking.py, lidar_parser.py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]
2025-09-01 rage baited by the world why the heck did it take me a whole 1.5 weekends to figure out 2 sensors trolled by the world bruv its joeber
2025-09-02 lidar wall following works
2025-09-07 added in assembly instructions
2025-09-07 steer system
2025-09-07 camera preprocessing images
2025-09-08 added servo specs
2025-09-08 lidar wall follow
2025-09-10 idk just let me switch branches
